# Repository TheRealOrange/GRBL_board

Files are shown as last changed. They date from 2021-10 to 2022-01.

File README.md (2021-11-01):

# GRBL_board

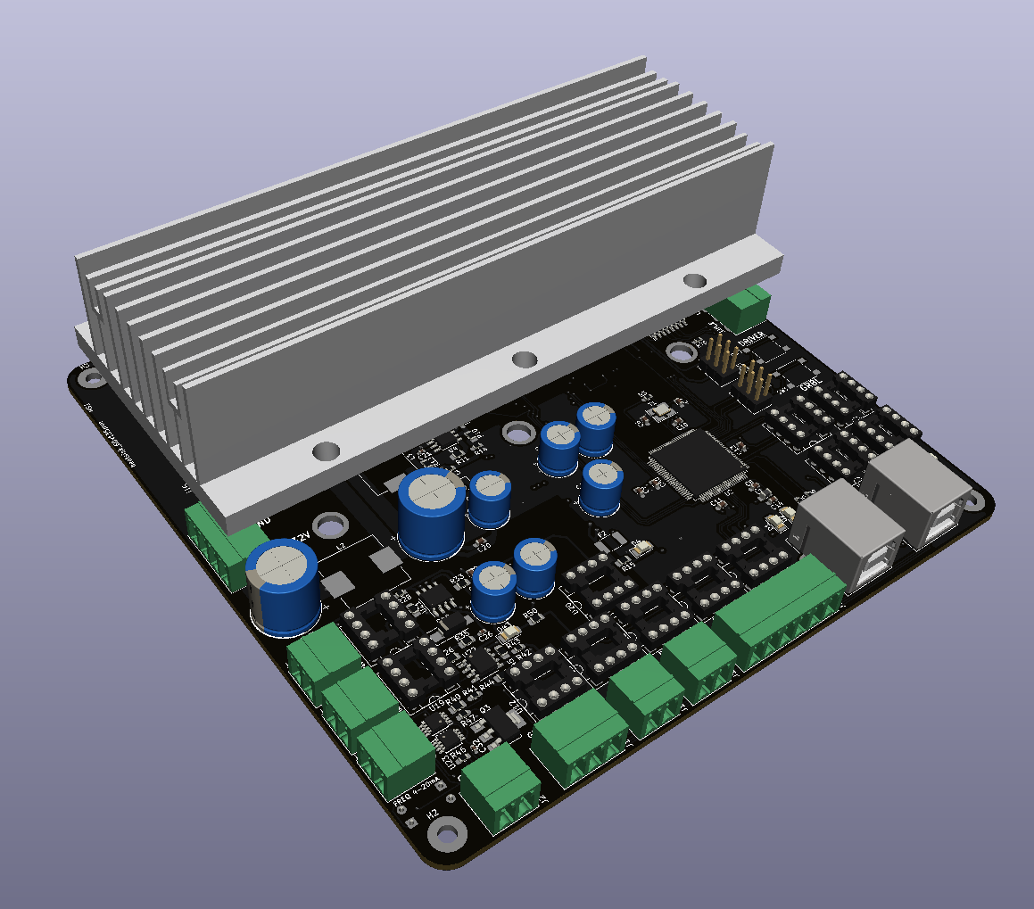
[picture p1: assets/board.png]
pcb picture


## Introduction

This is a PCB designed to run [GRBL](https://github.com/gnea/grbl), an open source CNC control software that is designed and optimised for Arduino. This board uses [GRBL-Mega](https://github.com/gnea/grbl-Mega), which is a version of GRBL that can run on the ATMEGA-2560, used in the Arduino Mega. This implementation allows GRBL to have a larger buffer size, since the ATMEGA-328P that GRBL was originally designed for has severe memory limitations.

This board design incorporates several additional features, such as:

- Designed for SPI configured Trinamic stepper drivers such as the TMC5160, TMC2130, etc.
- Ability to change the mirrored axis (X, Y or Z) via software (supports software configurable gantry levelling)
- All inputs and limit switch inputs wired with optocouplers, designed for normally open switches
- Onboard 12V 2A regulator, accepting 20-32VDC input
- Speed control for industrial VFDs, with a standard 4-20mA current loop for spindle speed control
- Sink logic for spindle control
- Possible sensorless homing using Trinamic drivers (not ideal since it only emulates a limit switch)

The goal is to accomplish this with minimal editing of the GRBL code, thus to do so an additional ATMEGA-328P is added on the board to enable the additional features.

## Connections

This board is designed with the aim of being as compatible as possible with the default GRBL, and as such, the pins are wired to follow the default GRBL-Mega pinout, as shown.
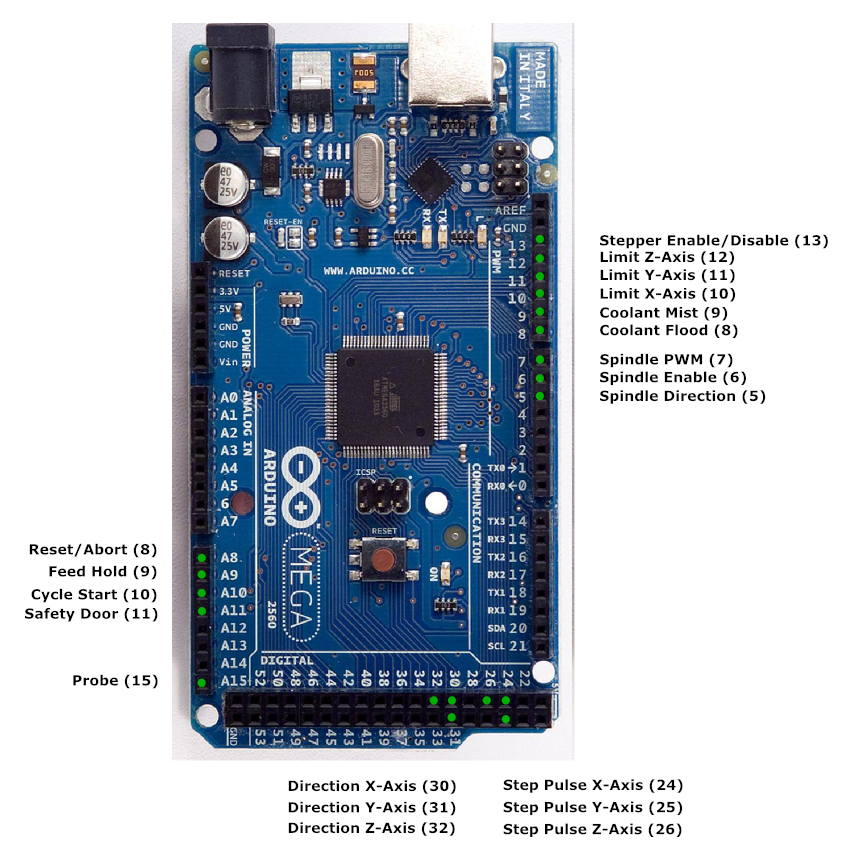
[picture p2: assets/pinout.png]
Default GRBL-Mega pinout


## Trinamic Drivers

Trinamic stepper motor drivers are exceptional in terms of performance and efficiency, incorporating advanced features that enable steppers to run cooler and with near silent operation. 

However, the tricky bit is that they are not a plug an play solution unlike other stepper drivers like the DRV8825 or the A4988 drivers. The drivers haveto be configured whenever they are powered up. To accomplish this, the separate ATMEGA-328P is used to communicate with the drivers via SPI in order to configure them.

## Mirrored Axis

Most CNC configurations include one axis which has dual stepper drive. GRBL has limited support for axis mirroring, and usually sacrifices some pins, such as spindle speed control. Thus, via the use of multiplexer ICs and the separate ATMEGA-328P, code can be uploaded to the ATMEGA-328P in order to specify which axis to mirror and whether to do gantry levelling for that axis.

To accomplish gantry levelling, the ATMEGA-328P will check the two limit switches on the mirrored axis, and if only one switch is triggered, the corresponding stepper's STEP pin will be held low, preventing it from moving until both switches are triggered. Once both limit switches are triggered, the limit switch signal will be sent to the GRBL controller running on the ATMEGA-2560.

## Inputs

Previously, I had an extremely bad experience with EMI on the limit switch lines when building a CNC, thus I decided to include an optocoupler on each input of the CNC controller. Although the switches are still normally open, the optocoupler requires current to drive the LED and thus it is nearly impossible for EMI to trigger the optocoupler. This should make the CNC much more robust against EMI, and it is possible to change the switches to normally closed by modifying GRBL.

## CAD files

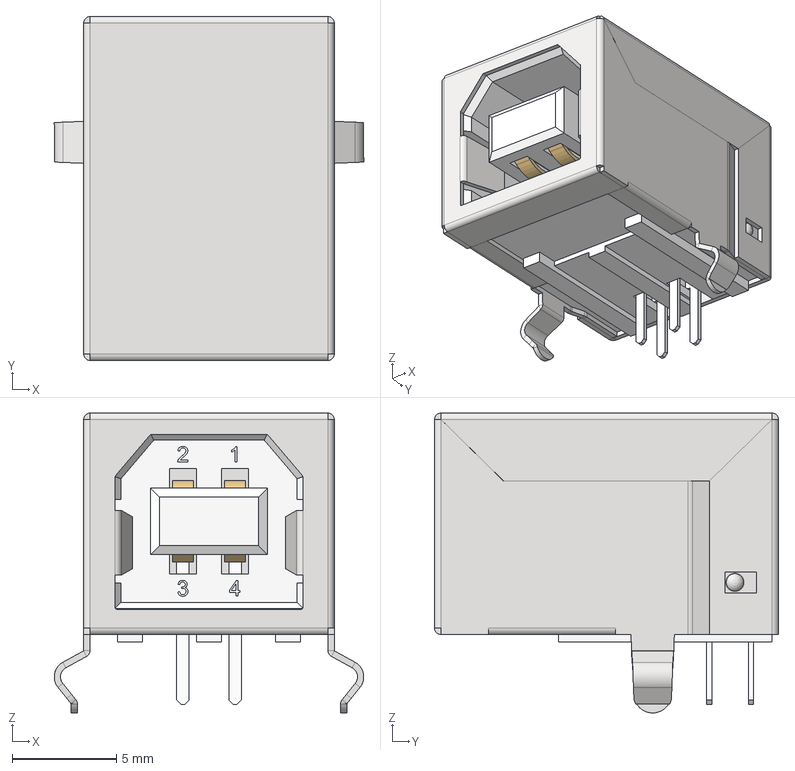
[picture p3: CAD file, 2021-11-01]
grbl_board/3d/USB_B_Horizontal.stp
14.8 x 16.5 x 14.4 mm

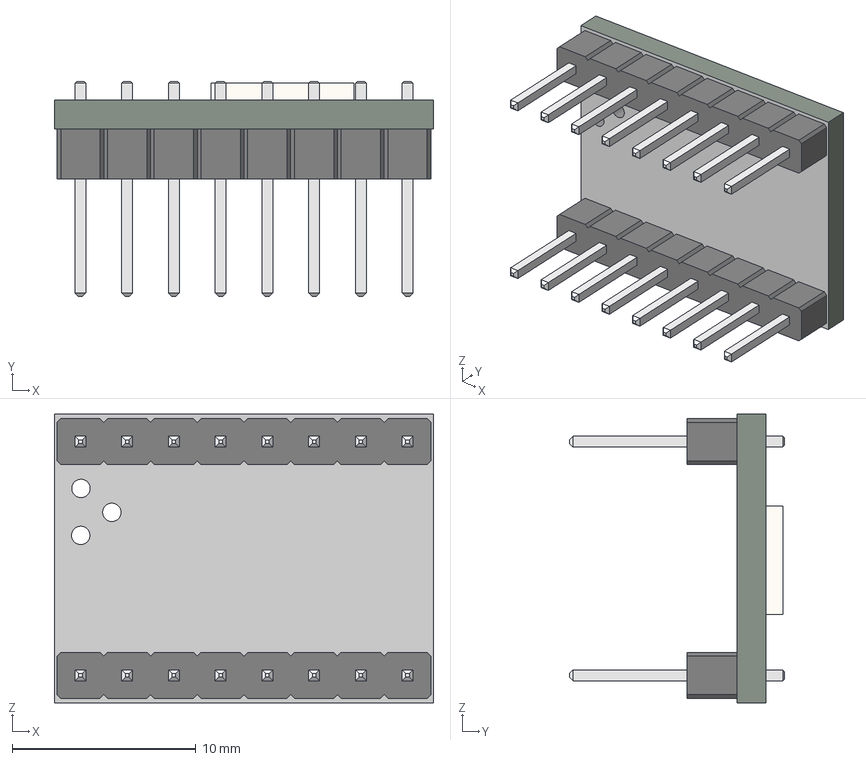
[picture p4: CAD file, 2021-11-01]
grbl_board/3d/SilentStepStick.step
20.6 x 11.7 x 15.7 mm

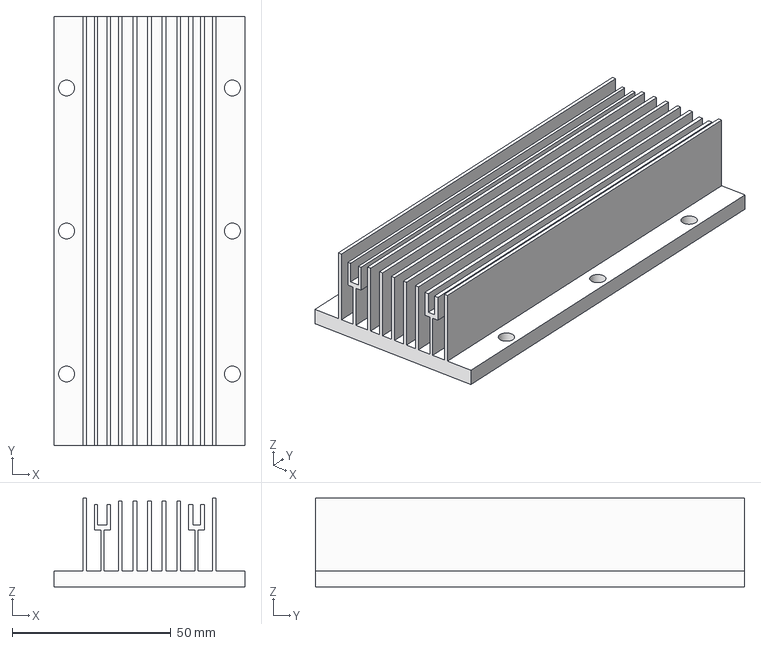
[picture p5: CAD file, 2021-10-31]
grbl_board/3d/heatsink_60x135mm_v1.step
60.0 x 135.0 x 28.0 mm

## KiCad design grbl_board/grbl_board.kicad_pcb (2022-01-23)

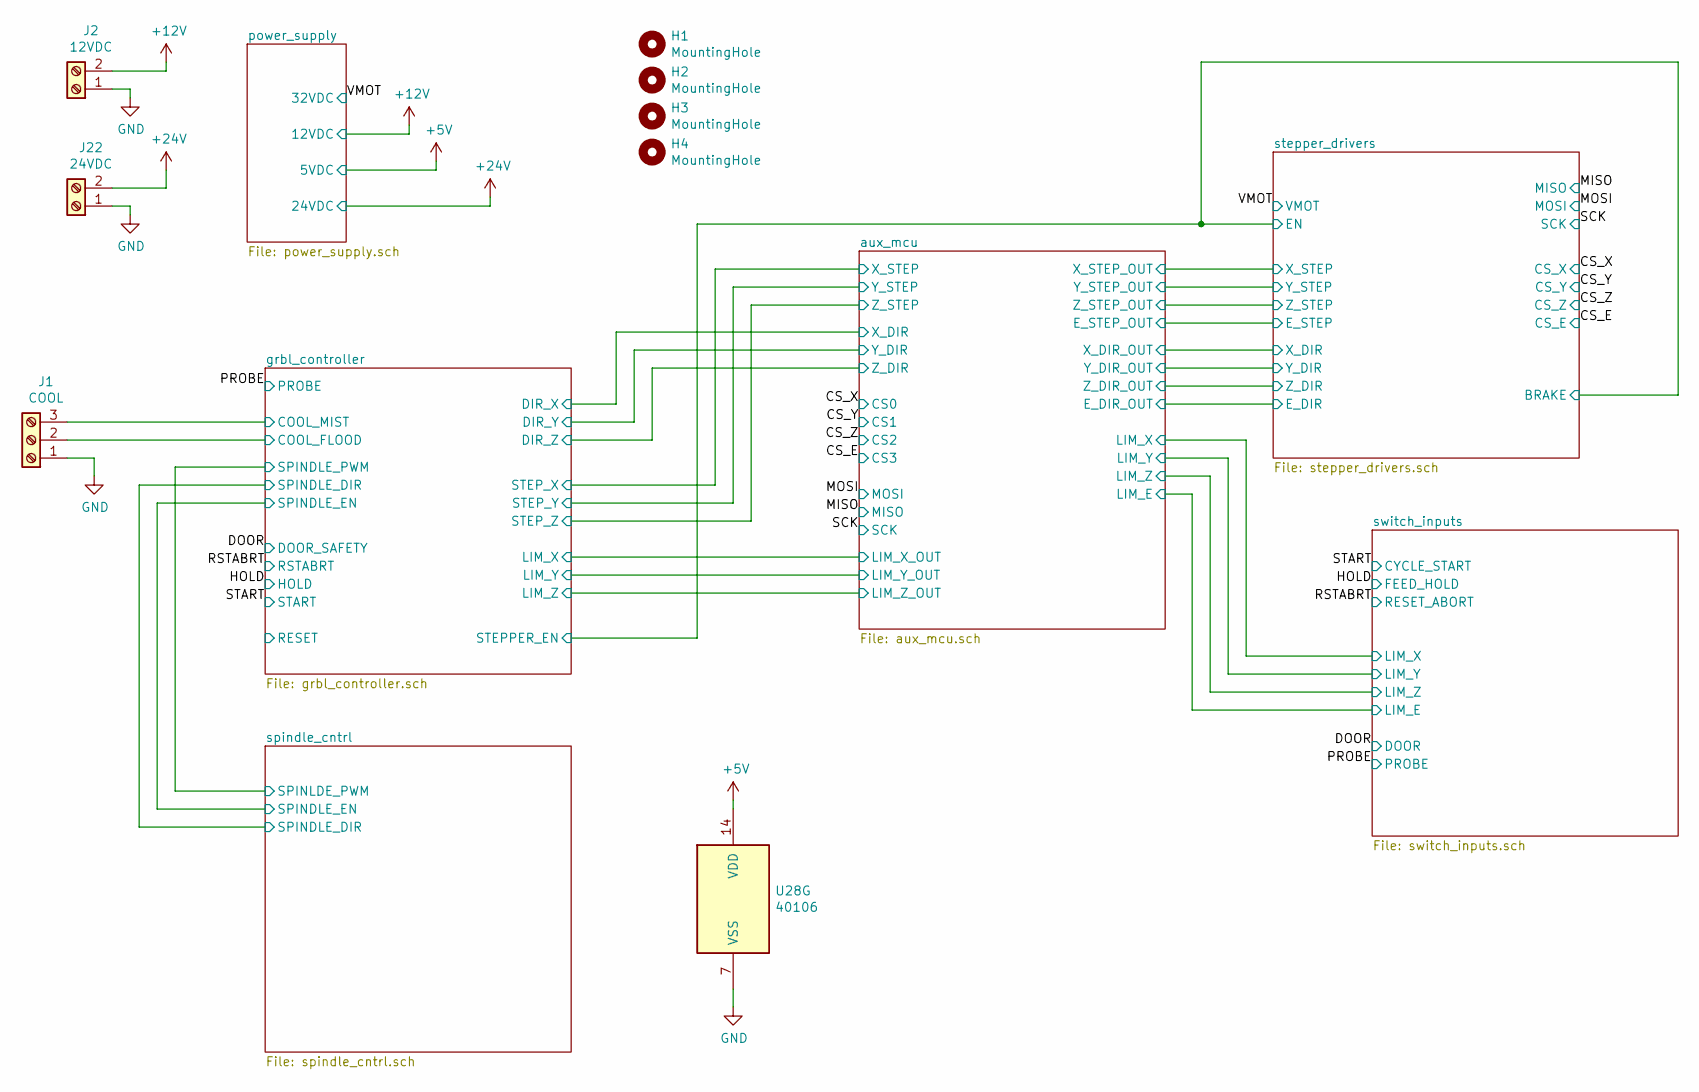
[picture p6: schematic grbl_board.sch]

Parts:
H1, H2, H3, H4: MountingHole; MountingHole_3.2mm_M3_Pad
J1: COOL; PhoenixContact_MC_1,5_3-G-3.81_1x03_P3.81mm_Horizontal; Digikey Part No. ED2809-ND
J2: 12VDC; PhoenixContact_MC_1,5_2-G-3.81_1x02_P3.81mm_Horizontal; Digikey Part No. ED2808-ND
J22: 24VDC; PhoenixContact_MC_1,5_2-G-3.81_1x02_P3.81mm_Horizontal; Digikey Part No. ED2808-ND
U28: 40106; TSSOP-14_4.4x5mm_P0.65mm; Digikey Part No. HEF40106BTT,112-ND

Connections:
+5V: U28.14 (VDD); also elsewhere on the board
+12V: J2.2; also elsewhere on the board
+24V: J22.2; also elsewhere on the board
/grbl_controller/COOL_FLOOD: J1.2; also elsewhere on the board
/grbl_controller/COOL_MIST: J1.3; also elsewhere on the board
GND: J1.1, J2.1, J22.1, U28.7 (VSS); also elsewhere on the board

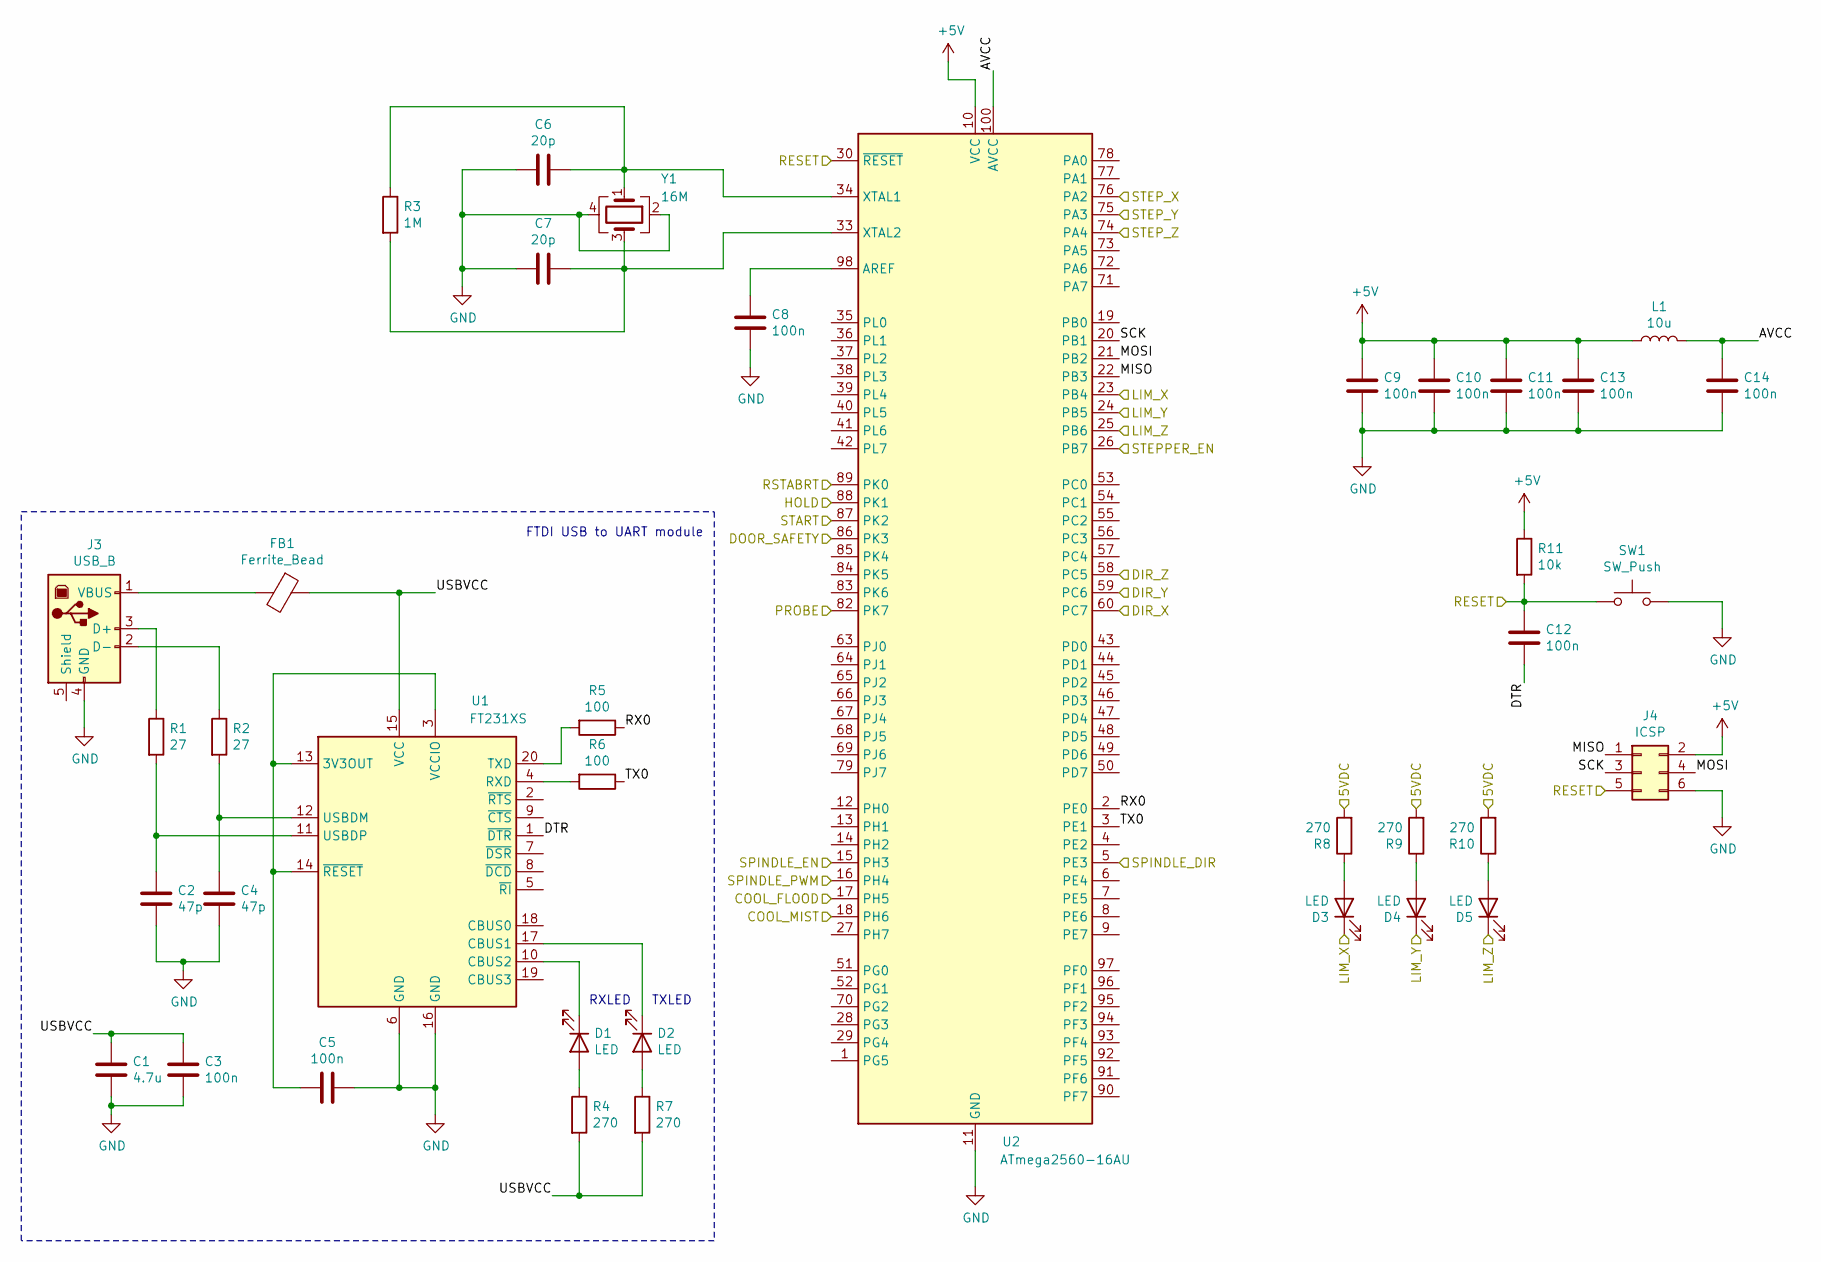
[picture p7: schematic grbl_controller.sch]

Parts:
C1: 4.7u; C_1206_3216Metric_Pad1.33x1.80mm_HandSolder; Digikey Part No. 1276-6781-1-ND
C2, C4: 47p; C_0402_1005Metric_Pad0.74x0.62mm_HandSolder; Digikey Part No. 1276-1699-1-ND
C3, C5, C8, C9, C10, C11, C12, C13, C14: 100n; C_0603_1608Metric_Pad1.05x0.95mm_HandSolder; Digikey Part No. 1276-1941-1-ND
C6, C7: 20p; C_0603_1608Metric_Pad1.05x0.95mm_HandSolder; Digikey Part No. 1276-1187-1-ND
D1, D2: LED; LED_1206_3216Metric_Pad1.42x1.75mm_HandSolder; Digikey Part No. 404-1042-1-ND
D3, D4, D5: LED; LED_1206_3216Metric_Pad1.42x1.75mm_HandSolder; Digikey Part No. 404-1046-1-ND
FB1: Ferrite_Bead; C_0603_1608Metric_Pad1.05x0.95mm_HandSolder; Digikey Part No. 732-1591-1-ND
J3: USB_B; USB_B_OST_USB-B1HSxx_Horizontal; Digikey Part No. 380-1492-ND
J4: ICSP; PinHeader_2x03_P2.54mm_Vertical; Digikey Part No. 609-3234-ND
L1: 10u; L_0805_2012Metric_Pad1.05x1.20mm_HandSolder; Digikey Part No. 490-4029-1-ND
R1, R2: 27; R_0603_1608Metric_Pad0.98x0.95mm_HandSolder; Digikey Part No. 311-27GRCT-ND
R3: 1M; R_0603_1608Metric_Pad0.98x0.95mm_HandSolder; Digikey Part No. 311-1.0MGRCT-ND
R4, R7, R8, R9, R10: 270; R_0805_2012Metric_Pad1.15x1.40mm_HandSolder; Digikey Part No. YAG6172CT-ND
R5, R6: 100; R_0603_1608Metric_Pad0.98x0.95mm_HandSolder; Digikey Part No. 311-100GRCT-ND
R11: 10k; R_0805_2012Metric_Pad1.15x1.40mm_HandSolder; Digikey Part No. 311-10KARCT-ND
SW1: SW_Push; SW_Push_1P1T_NO_6x6mm_H9.5mm; Digikey Part No. EG2526CT-ND
U1: FT231XS; SSOP-20_3.9x8.7mm_P0.635mm; Digikey Part No. 768-1129-1-ND
U2: ATmega2560-16AU; TQFP-100_14x14mm_P0.5mm; Digikey Part No. ATMEGA2560-16AU-ND
Y1: 16M; Crystal_SMD_SeikoEpson_TSX3225-4Pin_3.2x2.5mm_HandSoldering; Digikey Part No. SER4372CT-ND

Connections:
+5V: C9.1, C10.1, C11.1, C13.1, J4.2, L1.1, R11.1, U2.10 (VCC), U2.31 (VCC), U2.61 (VCC), U2.80 (VCC); also elsewhere on the board
/DOOR: U2.86 (PK3); also elsewhere on the board
/HOLD: U2.88 (PK1); also elsewhere on the board
/PROBE: U2.82 (PK7); also elsewhere on the board
/RSTABRT: U2.89 (PK0); also elsewhere on the board
/START: U2.87 (PK2); also elsewhere on the board
/grbl_controller/5VDC: R8.2, R9.2, R10.2
/grbl_controller/AVCC: C14.1, L1.2, U2.100 (AVCC)
/grbl_controller/COOL_FLOOD: U2.17 (PH5); also elsewhere on the board
/grbl_controller/COOL_MIST: U2.18 (PH6); also elsewhere on the board
/grbl_controller/DIR_X: U2.60 (PC7); also elsewhere on the board
/grbl_controller/DIR_Y: U2.59 (PC6); also elsewhere on the board
/grbl_controller/DIR_Z: U2.58 (PC5); also elsewhere on the board
/grbl_controller/DTR: C12.2, U1.1 (~DTR)
/grbl_controller/LIM_X: D3.1 (K), U2.23 (PB4); also elsewhere on the board
/grbl_controller/LIM_Y: D4.1 (K), U2.24 (PB5); also elsewhere on the board
/grbl_controller/LIM_Z: D5.1 (K), U2.25 (PB6); also elsewhere on the board
/grbl_controller/MISO: J4.1, U2.22 (PB3)
/grbl_controller/MOSI: J4.4, U2.21 (PB2)
/grbl_controller/RESET: C12.1, J4.5, R11.2, SW1.1, U2.30 (~RESET)
/grbl_controller/RX0: R5.1, U2.2 (PE0)
/grbl_controller/SCK: J4.3, U2.20 (PB1)
/grbl_controller/SPINDLE_DIR: U2.5 (PE3); also elsewhere on the board
/grbl_controller/SPINDLE_EN: U2.15 (PH3); also elsewhere on the board
/grbl_controller/SPINDLE_PWM: U2.16 (PH4); also elsewhere on the board
/grbl_controller/STEP_X: U2.76 (PA2); also elsewhere on the board
/grbl_controller/STEP_Y: U2.75 (PA3); also elsewhere on the board
/grbl_controller/STEP_Z: U2.74 (PA4); also elsewhere on the board
/grbl_controller/TX0: R6.1, U2.3 (PE1)
/grbl_controller/USBVCC: C1.1, C3.1, FB1.1, R4.2, R7.2, U1.15 (VCC)
/stepper_drivers/BRAKE: U2.26 (PB7); also elsewhere on the board
GND: C1.2, C2.2, C3.2, C4.2, C5.1, C6.2, C7.2, C8.1, C9.2, C10.2, C11.2, C13.2, C14.2, J3.4 (GND), J4.6, SW1.2, U1.6 (GND), U1.16 (GND), U2.11 (GND), U2.32 (GND), U2.62 (GND), U2.81 (GND), U2.99 (GND), Y1.2, Y1.4; also elsewhere on the board
unnamed: C2.1, R1.2, U1.11 (USBDP)
unnamed: C4.1, R2.2, U1.12 (USBDM)
unnamed: C5.2, U1.3 (VCCIO), U1.13 (3V3OUT), U1.14 (~RESET)
unnamed: C6.1, R3.1, U2.34 (XTAL1), Y1.1
unnamed: C7.1, R3.2, U2.33 (XTAL2), Y1.3
unnamed: C8.2, U2.98 (AREF)
unnamed: D1.1 (K), U1.10 (CBUS2)
unnamed: D1.2 (A), R4.1
unnamed: D2.1 (K), U1.17 (CBUS1)
unnamed: D2.2 (A), R7.1
unnamed: D3.2 (A), R8.1
unnamed: D4.2 (A), R9.1
unnamed: D5.2 (A), R10.1
unnamed: FB1.2, J3.1 (VBUS)
unnamed: J3.2 (D-), R2.1
unnamed: J3.3 (D+), R1.1
unnamed: R5.2, U1.20 (TXD)
unnamed: R6.2, U1.4 (RXD)

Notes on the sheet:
TXLED
RXLED
FTDI USB to UART module

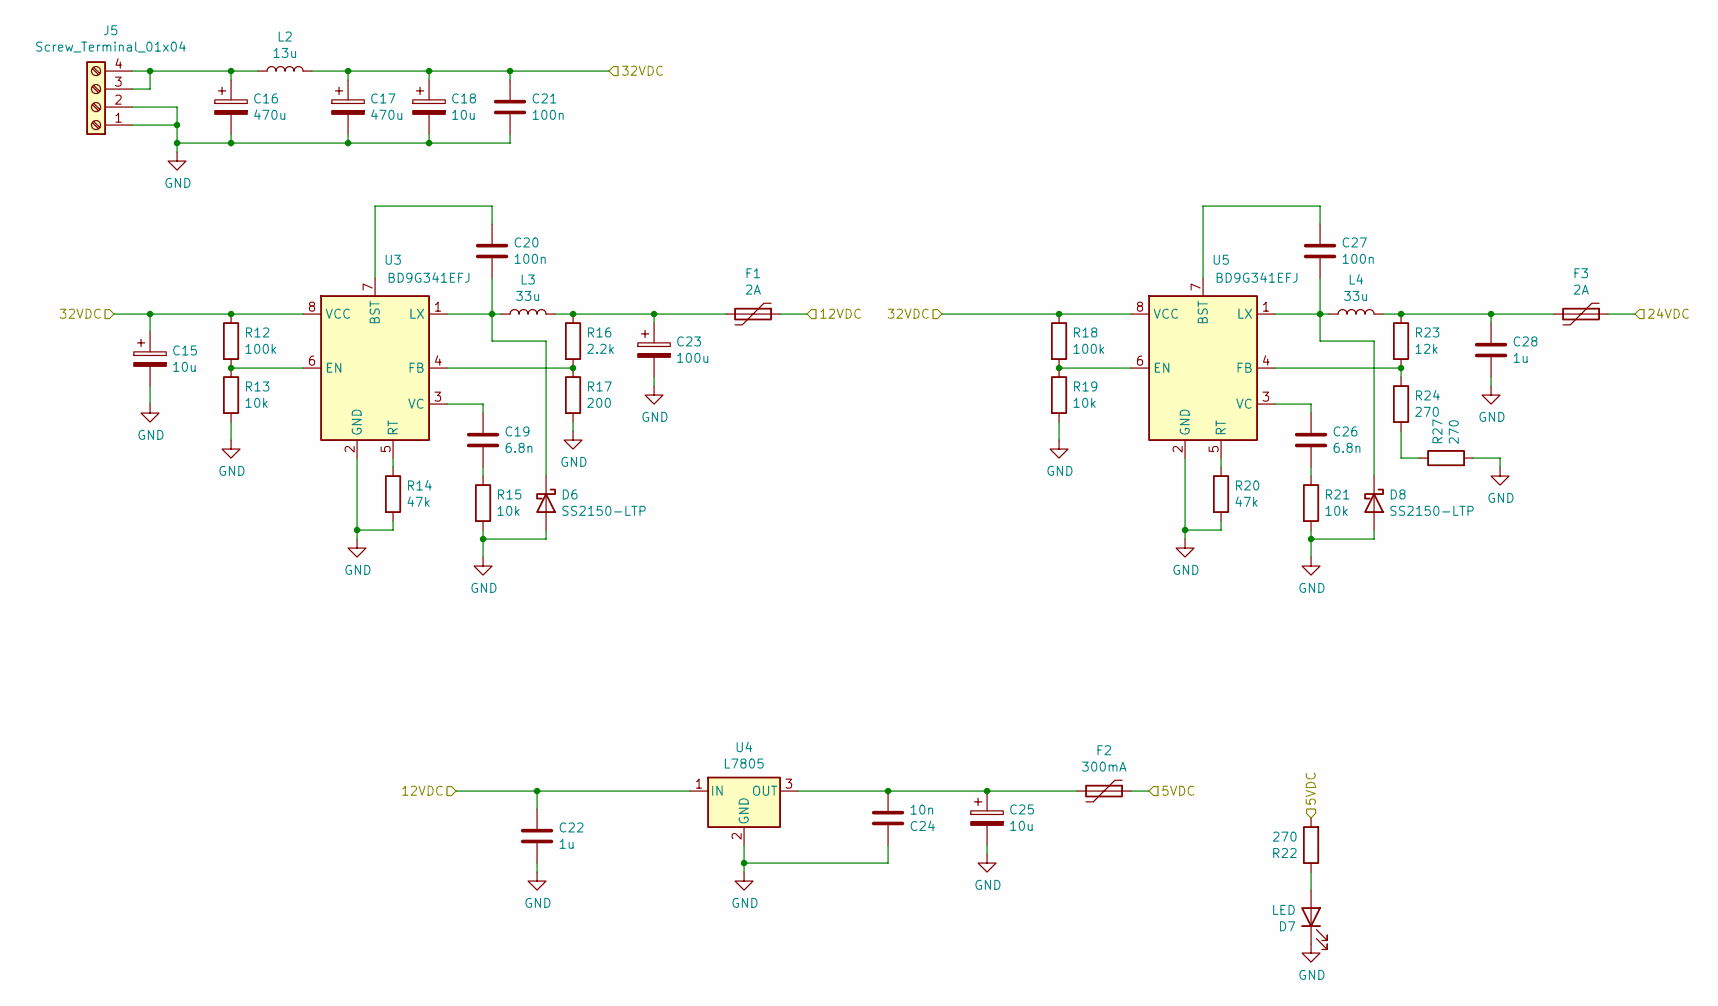
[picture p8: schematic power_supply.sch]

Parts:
C15, C18, C25: 10u; CP_Radial_D8.0mm_P3.50mm; Digikey Part No. 495-75596-ND
C16, C17: 470u; CP_Radial_D12.5mm_P5.00mm; Digikey Part No. 495-76603-ND
C19, C26: 6.8n; C_0402_1005Metric_Pad0.74x0.62mm_HandSolder; Digikey Part No. 1276-CL05B682KB5VPNCCT-ND
C20, C21, C27: 100n; C_0603_1608Metric_Pad1.05x0.95mm_HandSolder; Digikey Part No. 1276-1941-1-ND
C22, C28: 1u; C_1206_3216Metric_Pad1.33x1.80mm_HandSolder; Digikey Part No. 1276-1204-1-ND
C23: 100u; CP_Radial_D8.0mm_P3.50mm; Digikey Part No. 399-6119-ND
C24: 10n; C_0603_1608Metric_Pad1.08x0.95mm_HandSolder; Digikey Part No. 1276-1009-1-ND
D6, D8: SS2150-LTP; D_SMA_Handsoldering; Digikey Part No. SS2150-LTPMSCT-ND
D7: LED; LED_1206_3216Metric_Pad1.42x1.75mm_HandSolder; Digikey Part No. 404-1046-1-ND
F1, F3: 2A; Fuse_Bourns_MF-RHT200; Digikey Part No. 118-MF-RHT200/32-0-ND
F2: 300mA; Fuse_1812_4532Metric_Castellated; Digikey Part No. 507-1758-1-ND
J5: Screw_Terminal_01x04; PhoenixContact_MC_1,5_4-G-3.81_1x04_P3.81mm_Horizontal; Digikey Part No. ED2810-ND
L2: 13u; L_Wuerth_HCI-1365; Digikey Part No. 732-1140-1-ND
L3, L4: 33u; L_Vishay_IHLP-4040; Digikey Part No. 541-2273-1-ND
R12, R18: 100k; R_0603_1608Metric_Pad0.98x0.95mm_HandSolder; Digikey Part No. 311-100KGRCT-ND
R13, R15, R19, R21: 10k; R_0805_2012Metric_Pad1.15x1.40mm_HandSolder; Digikey Part No. 311-10KARCT-ND
R14, R20: 47k; R_0805_2012Metric_Pad1.15x1.40mm_HandSolder; Digikey Part No. 311-47KARCT-ND
R16: 2.2k; R_0603_1608Metric_Pad0.98x0.95mm_HandSolder; Digikey Part No. 311-2.2KGRCT-ND
R17: 200; R_0603_1608Metric_Pad0.98x0.95mm_HandSolder; Digikey Part No. 311-200GRCT-ND
R22, R24, R27: 270; R_0805_2012Metric_Pad1.15x1.40mm_HandSolder; Digikey Part No. YAG6172CT-ND
R23: 12k; R_0805_2012Metric_Pad1.15x1.40mm_HandSolder; Digikey Part No. 311-12KARCT-ND
U3, U5: BD9G341EFJ; HTSOP-8-1EP_3.9x4.9mm_P1.27mm_EP2.4x3.2mm_ThermalVias; Digikey Part No. BD9G341AEFJ-E2CT-ND
U4: L7805; TO-263-2; Digikey Part No. 497-1170-1-ND

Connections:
+5V: F2.1, R22.2; also elsewhere on the board
+12V: C22.1, F1.1, U4.1 (IN); also elsewhere on the board
+24V: F3.1; also elsewhere on the board
/VMOT: C15.1, C17.1, C18.1, C21.1, L2.2, R12.1, R18.1, U3.8 (VCC), U5.8 (VCC); also elsewhere on the board
GND: C15.2, C16.2, C17.2, C18.2, C21.2, C22.2, C23.2, C24.1, C25.2, C28.2, D6.2 (A), D7.1 (K), D8.2 (A), J5.1, J5.2, R13.2, R14.2, R15.2, R17.2, R19.2, R20.2, R21.2, R27.2, U3.2 (GND), U4.2 (GND), U5.2 (GND); also elsewhere on the board
unnamed: C16.1, J5.3, J5.4, L2.1
unnamed: C19.1, U3.3 (VC)
unnamed: C19.2, R15.1
unnamed: C20.1, U3.7 (BST)
unnamed: C20.2, D6.1 (K), L3.1, U3.1 (LX)
unnamed: C23.1, F1.2, L3.2, R16.1
unnamed: C24.2, C25.1, F2.2, U4.3 (OUT)
unnamed: C26.1, U5.3 (VC)
unnamed: C26.2, R21.1
unnamed: C27.1, U5.7 (BST)
unnamed: C27.2, D8.1 (K), L4.1, U5.1 (LX)
unnamed: C28.1, F3.2, L4.2, R23.1
unnamed: D7.2 (A), R22.1
unnamed: R12.2, R13.1, U3.6 (EN)
unnamed: R14.1, U3.5 (RT)
unnamed: R16.2, R17.1, U3.4 (FB)
unnamed: R18.2, R19.1, U5.6 (EN)
unnamed: R20.1, U5.5 (RT)
unnamed: R23.2, R24.1, U5.4 (FB)
unnamed: R24.2, R27.1

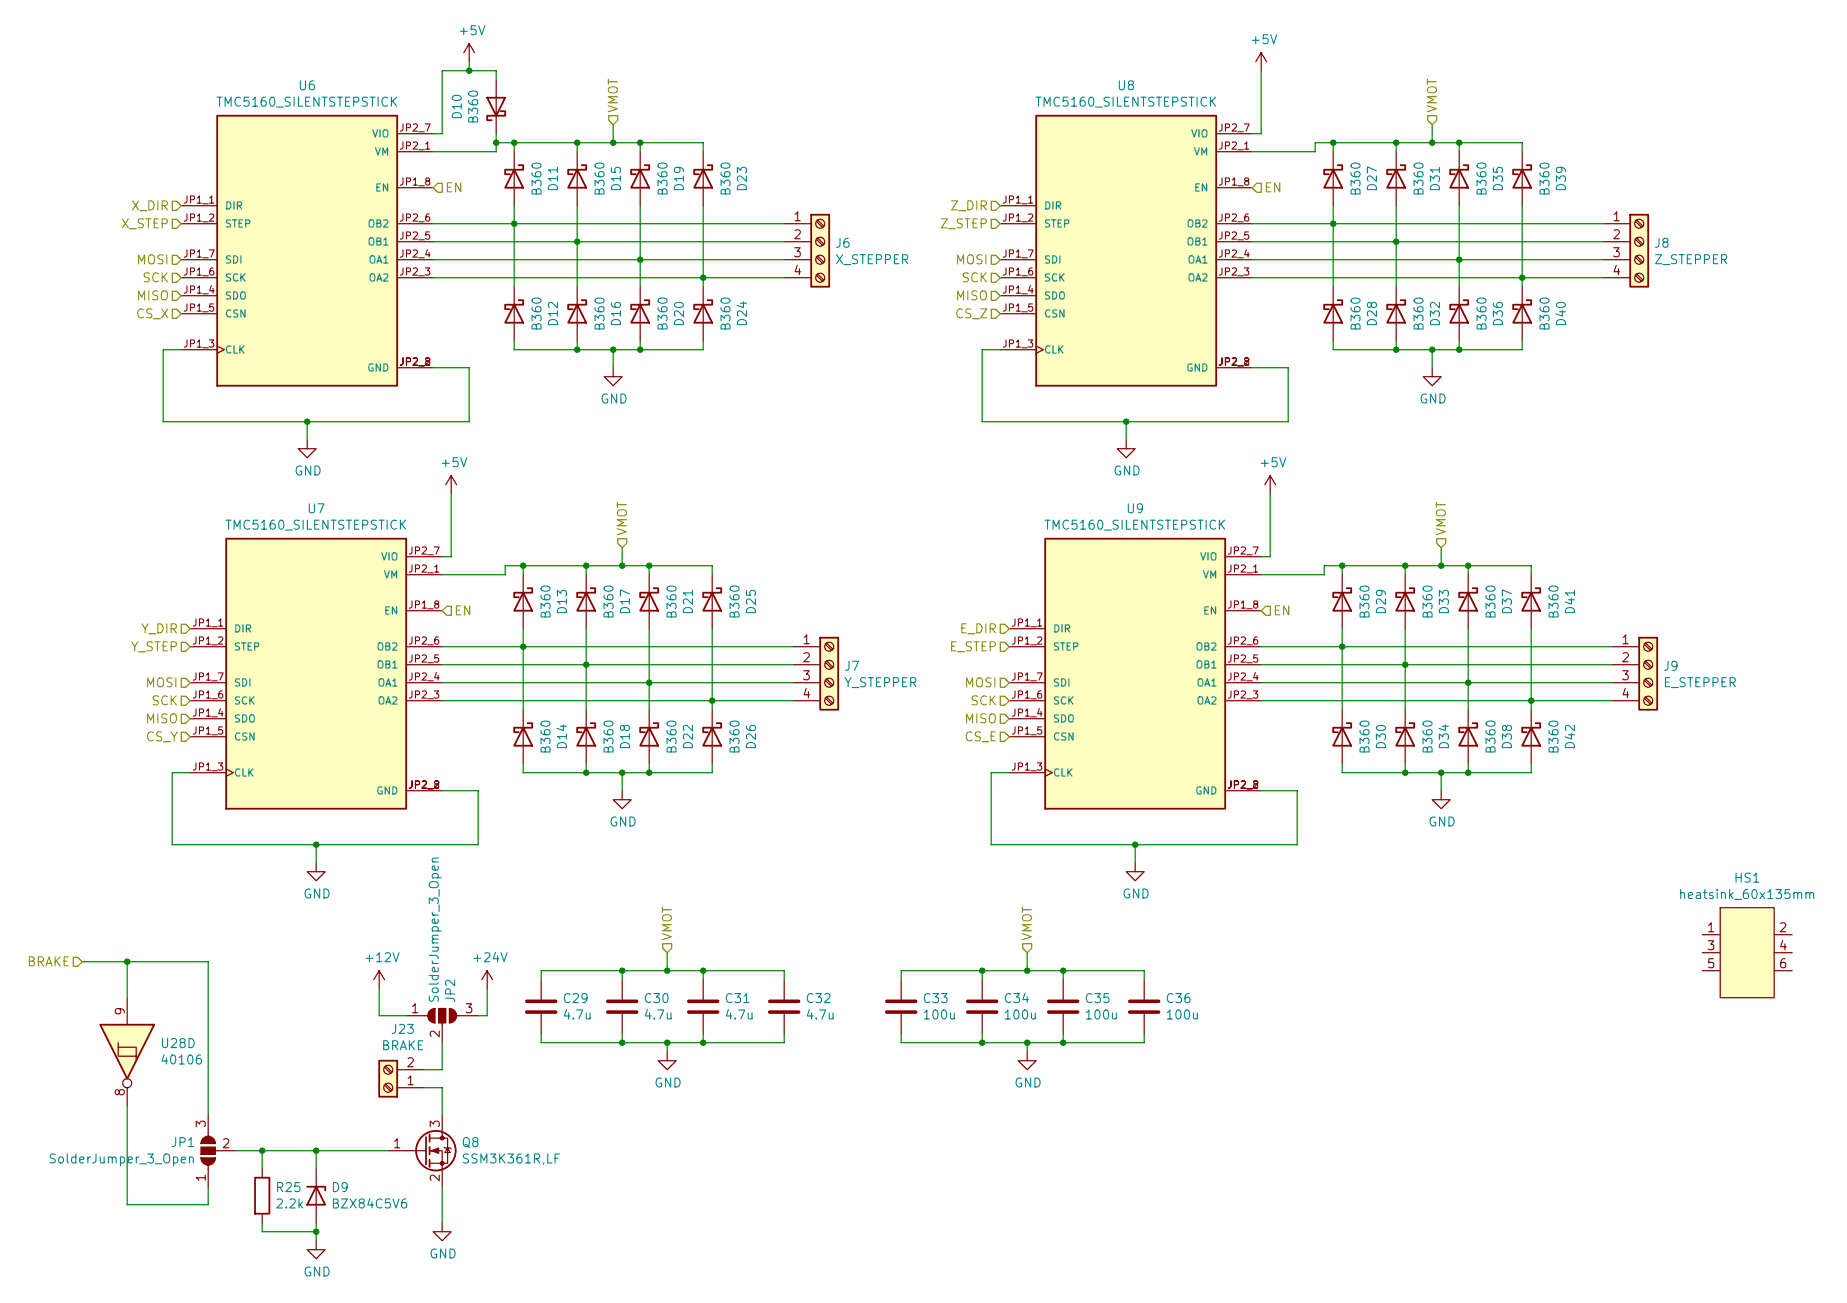
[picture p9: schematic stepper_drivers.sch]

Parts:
C29, C30, C31, C32: 4.7u; C_1206_3216Metric_Pad1.33x1.80mm_HandSolder; Digikey Part No. 1276-6781-1-ND
C33, C34, C35, C36: 100u; CP_Elec_8x10; Digikey Part No. UE107M050HFKTA
D9: BZX84C5V6; D_SOT-23_ANK; Digikey Part No. 1514-BZX84C5V6TRPBFREECT-ND
D10, D11, D12, D13, D14, D15, D16, D17, D18, D19, D20, D21, D22, D23, D24, D25, D26, D27, D28, D29, D30, D31, D32, D33, D34, D35, D36, D37, D38, D39, D40, D41, D42: B360; D_SMA_Handsoldering; Digikey Part No. CD214A-B360RCT-ND
HS1: heatsink_60x135mm
J6: X_STEPPER; PhoenixContact_MC_1,5_4-G-3.81_1x04_P3.81mm_Horizontal; Digikey Part No. ED2810-ND
J7: Y_STEPPER; PhoenixContact_MC_1,5_4-G-3.81_1x04_P3.81mm_Horizontal; Digikey Part No. ED2810-ND
J8: Z_STEPPER; PhoenixContact_MC_1,5_4-G-3.81_1x04_P3.81mm_Horizontal; Digikey Part No. ED2810-ND
J9: E_STEPPER; PhoenixContact_MC_1,5_4-G-3.81_1x04_P3.81mm_Horizontal; Digikey Part No. ED2810-ND
J23: BRAKE; PhoenixContact_MC_1,5_2-G-3.81_1x02_P3.81mm_Horizontal; Digikey Part No. ED2808-ND
JP1, JP2: SolderJumper_3_Open; SolderJumper-3_P1.3mm_Open_RoundedPad1.0x1.5mm
Q8: SSM3K361R,LF; SOT-23; Digikey Part No. SSM3K361RLFCT-ND
R25: 2.2k; R_0603_1608Metric_Pad0.98x0.95mm_HandSolder; Digikey Part No. 311-2.2KGRCT-ND
U6, U7, U8, U9: TMC5160_SILENTSTEPSTICK; PARTREV v11; Digikey Part No. 1460-TMC5160SILENTSTEPSTICK-ND
U28: 40106

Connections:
+5V: D10.2 (A), U6.JP2_7 (VIO), U7.JP2_7 (VIO), U8.JP2_7 (VIO), U9.JP2_7 (VIO); also elsewhere on the board
+12V: JP2.1 (A); also elsewhere on the board
+24V: JP2.3 (B); also elsewhere on the board
/CS_E: U9.JP1_5 (CSN); also elsewhere on the board
/CS_X: U6.JP1_5 (CSN); also elsewhere on the board
/CS_Y: U7.JP1_5 (CSN); also elsewhere on the board
/CS_Z: U8.JP1_5 (CSN); also elsewhere on the board
/MISO: U6.JP1_4 (SDO), U7.JP1_4 (SDO), U8.JP1_4 (SDO), U9.JP1_4 (SDO); also elsewhere on the board
/MOSI: U6.JP1_7 (SDI), U7.JP1_7 (SDI), U8.JP1_7 (SDI), U9.JP1_7 (SDI); also elsewhere on the board
/SCK: U6.JP1_6 (SCK), U7.JP1_6 (SCK), U8.JP1_6 (SCK), U9.JP1_6 (SCK); also elsewhere on the board
/VMOT: C29.1, C30.1, C31.1, C32.1, C33.1, C34.1, C35.1, C36.1, D10.1 (K), D11.1 (K), D13.1 (K), D15.1 (K), D17.1 (K), D19.1 (K), D21.1 (K), D23.1 (K), D25.1 (K), D27.1 (K), D29.1 (K), D31.1 (K), D33.1 (K), D35.1 (K), D37.1 (K), D39.1 (K), D41.1 (K), U6.JP2_1 (VM), U7.JP2_1 (VM), U8.JP2_1 (VM), U9.JP2_1 (VM); also elsewhere on the board
/grbl_controller/DIR_X: U6.JP1_1 (DIR); also elsewhere on the board
/grbl_controller/DIR_Y: U7.JP1_1 (DIR); also elsewhere on the board
/grbl_controller/DIR_Z: U8.JP1_1 (DIR); also elsewhere on the board
/stepper_drivers/BRAKE: JP1.3 (B), U6.JP1_8 (EN), U7.JP1_8 (EN), U8.JP1_8 (EN), U9.JP1_8 (EN), U28.9; also elsewhere on the board
/stepper_drivers/E_DIR: U9.JP1_1 (DIR); also elsewhere on the board
/stepper_drivers/E_STEP: U9.JP1_2 (STEP); also elsewhere on the board
/stepper_drivers/X_STEP: U6.JP1_2 (STEP); also elsewhere on the board
/stepper_drivers/Y_STEP: U7.JP1_2 (STEP); also elsewhere on the board
/stepper_drivers/Z_STEP: U8.JP1_2 (STEP); also elsewhere on the board
GND: C29.2, C30.2, C31.2, C32.2, C33.2, C34.2, C35.2, C36.2, D9.2 (A), D12.2 (A), D14.2 (A), D16.2 (A), D18.2 (A), D20.2 (A), D22.2 (A), D24.2 (A), D26.2 (A), D28.2 (A), D30.2 (A), D32.2 (A), D34.2 (A), D36.2 (A), D38.2 (A), D40.2 (A), D42.2 (A), Q8.2 (S), R25.2, U6.JP1_3 (CLK), U6.JP2_2 (GND), U6.JP2_8 (GND), U7.JP1_3 (CLK), U7.JP2_2 (GND), U7.JP2_8 (GND), U8.JP1_3 (CLK), U8.JP2_2 (GND), U8.JP2_8 (GND), U9.JP1_3 (CLK), U9.JP2_2 (GND), U9.JP2_8 (GND); also elsewhere on the board
unnamed: D9.1 (K), JP1.2 (C), Q8.1 (G), R25.1
unnamed: D11.2 (A), D12.1 (K), J6.1, U6.JP2_6 (OB2)
unnamed: D13.2 (A), D14.1 (K), J7.1, U7.JP2_6 (OB2)
unnamed: D15.2 (A), D16.1 (K), J6.2, U6.JP2_5 (OB1)
unnamed: D17.2 (A), D18.1 (K), J7.2, U7.JP2_5 (OB1)
unnamed: D19.2 (A), D20.1 (K), J6.3, U6.JP2_4 (OA1)
unnamed: D21.2 (A), D22.1 (K), J7.3, U7.JP2_4 (OA1)
unnamed: D23.2 (A), D24.1 (K), J6.4, U6.JP2_3 (OA2)
unnamed: D25.2 (A), D26.1 (K), J7.4, U7.JP2_3 (OA2)
unnamed: D27.2 (A), D28.1 (K), J8.1, U8.JP2_6 (OB2)
unnamed: D29.2 (A), D30.1 (K), J9.1, U9.JP2_6 (OB2)
unnamed: D31.2 (A), D32.1 (K), J8.2, U8.JP2_5 (OB1)
unnamed: D33.2 (A), D34.1 (K), J9.2, U9.JP2_5 (OB1)
unnamed: D35.2 (A), D36.1 (K), J8.3, U8.JP2_4 (OA1)
unnamed: D37.2 (A), D38.1 (K), J9.3, U9.JP2_4 (OA1)
unnamed: D39.2 (A), D40.1 (K), J8.4, U8.JP2_3 (OA2)
unnamed: D41.2 (A), D42.1 (K), J9.4, U9.JP2_3 (OA2)
unnamed: J23.1, Q8.3 (D)
unnamed: J23.2, JP2.2 (C)
unnamed: JP1.1 (A), U28.8

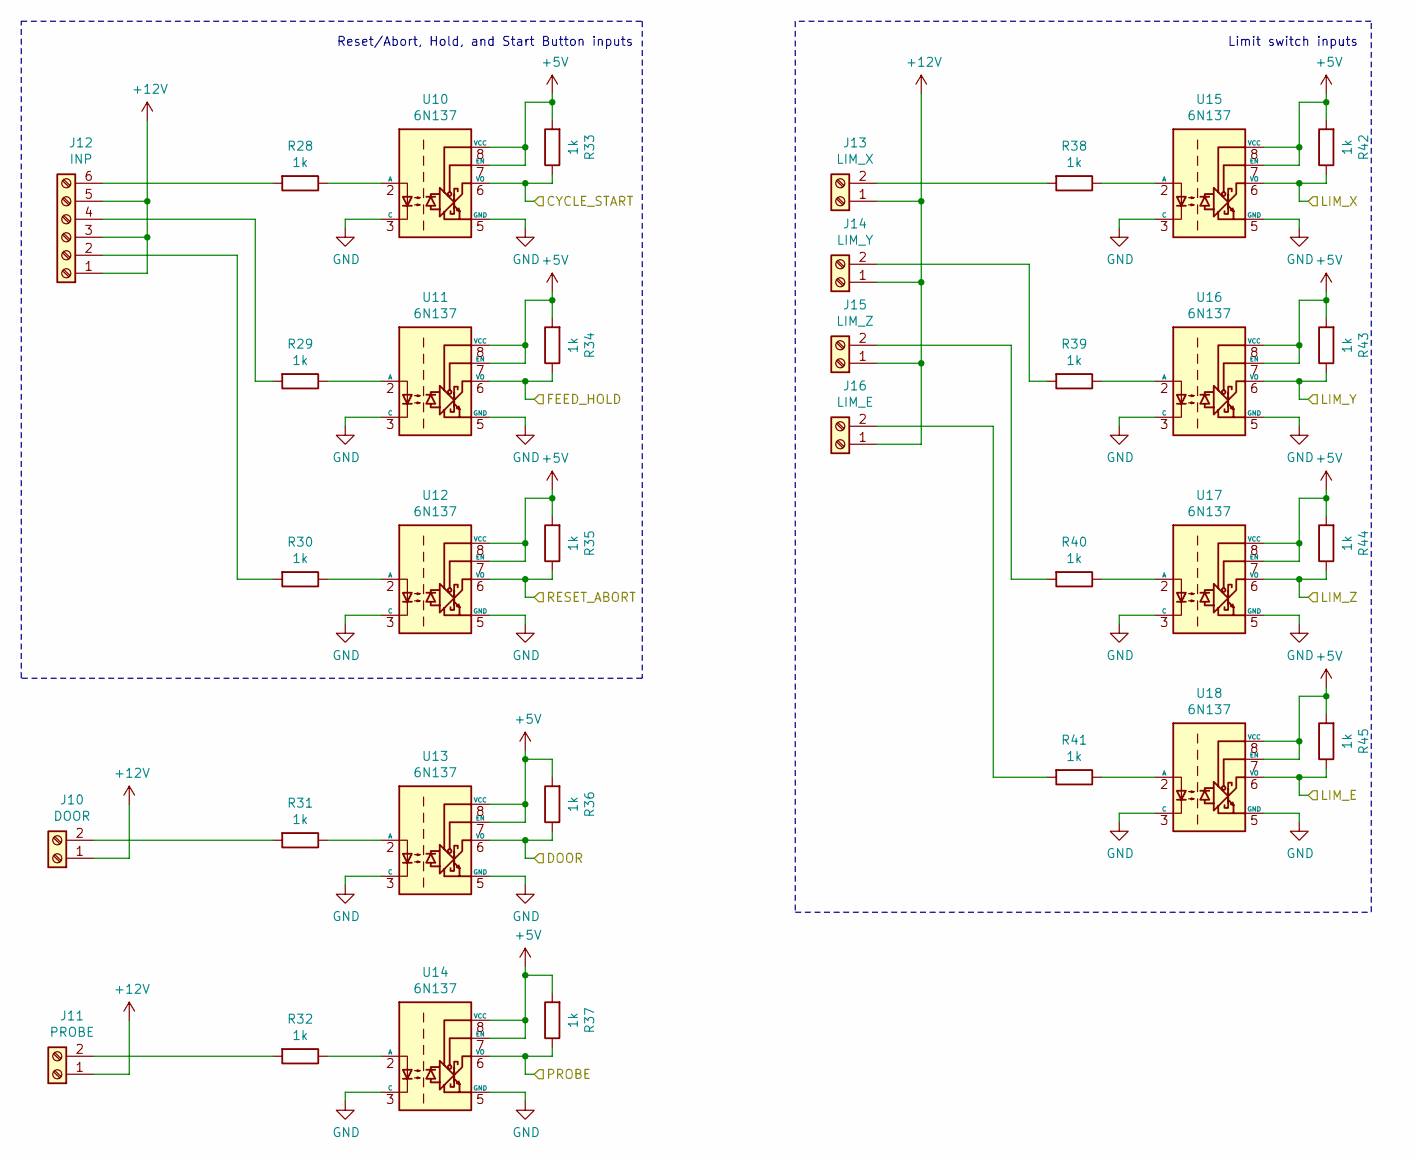
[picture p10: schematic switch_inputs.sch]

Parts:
J10: DOOR; PhoenixContact_MC_1,5_2-G-3.81_1x02_P3.81mm_Horizontal; Digikey Part No. ED2808-ND
J11: PROBE; PhoenixContact_MC_1,5_2-G-3.81_1x02_P3.81mm_Horizontal; Digikey Part No. ED2808-ND
J12: INP; PhoenixContact_MC_1,5_6-G-3.81_1x06_P3.81mm_Horizontal; Digikey Part No. ED2812-ND
J13: LIM_X; PhoenixContact_MC_1,5_2-G-3.81_1x02_P3.81mm_Horizontal; Digikey Part No. ED2808-ND
J14: LIM_Y; PhoenixContact_MC_1,5_2-G-3.81_1x02_P3.81mm_Horizontal; Digikey Part No. ED2808-ND
J15: LIM_Z; PhoenixContact_MC_1,5_2-G-3.81_1x02_P3.81mm_Horizontal; Digikey Part No. ED2808-ND
J16: LIM_E; PhoenixContact_MC_1,5_2-G-3.81_1x02_P3.81mm_Horizontal; Digikey Part No. ED2808-ND
R28, R29, R30, R31, R32, R38, R39, R40, R41: 1k; R_1206_3216Metric_Pad1.30x1.75mm_HandSolder; Digikey Part No. 311-1.0KERCT-ND
R33, R34, R35, R36, R37, R42, R43, R44, R45: 1k; R_0805_2012Metric_Pad1.15x1.40mm_HandSolder; Digikey Part No. 311-10KARCT-ND
U10, U11, U12, U13, U14, U15, U16, U17, U18: 6N137; DIP-8_W7.62mm_Socket; Digikey Part No. 6N137IS-ND

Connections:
+5V: R33.2, R34.2, R35.2, R36.2, R37.2, R42.2, R43.2, R44.2, R45.2, U10.7 (EN), U10.8 (VCC), U11.7 (EN), U11.8 (VCC), U12.7 (EN), U12.8 (VCC), U13.7 (EN), U13.8 (VCC), U14.7 (EN), U14.8 (VCC), U15.7 (EN), U15.8 (VCC), U16.7 (EN), U16.8 (VCC), U17.7 (EN), U17.8 (VCC), U18.7 (EN), U18.8 (VCC); also elsewhere on the board
+12V: J10.1, J11.1, J12.1, J12.3, J12.5, J13.1, J14.1, J15.1, J16.1; also elsewhere on the board
/DOOR: R36.1, U13.6 (VO); also elsewhere on the board
/HOLD: R34.1, U11.6 (VO); also elsewhere on the board
/PROBE: R37.1, U14.6 (VO); also elsewhere on the board
/RSTABRT: R35.1, U12.6 (VO); also elsewhere on the board
/START: R33.1, U10.6 (VO); also elsewhere on the board
/aux_mcu/LIM_E: R45.1, U18.6 (VO); also elsewhere on the board
/aux_mcu/LIM_X: R42.1, U15.6 (VO); also elsewhere on the board
/aux_mcu/LIM_Y: R43.1, U16.6 (VO); also elsewhere on the board
/aux_mcu/LIM_Z: R44.1, U17.6 (VO); also elsewhere on the board
GND: U10.3 (C), U10.5 (GND), U11.3 (C), U11.5 (GND), U12.3 (C), U12.5 (GND), U13.3 (C), U13.5 (GND), U14.3 (C), U14.5 (GND), U15.3 (C), U15.5 (GND), U16.3 (C), U16.5 (GND), U17.3 (C), U17.5 (GND), U18.3 (C), U18.5 (GND); also elsewhere on the board
unnamed: J10.2, R31.2
unnamed: J11.2, R32.2
unnamed: J12.2, R30.2
unnamed: J12.4, R29.2
unnamed: J12.6, R28.2
unnamed: J13.2, R38.2
unnamed: J14.2, R39.2
unnamed: J15.2, R40.2
unnamed: J16.2, R41.2
unnamed: R28.1, U10.2 (A)
unnamed: R29.1, U11.2 (A)
unnamed: R30.1, U12.2 (A)
unnamed: R31.1, U13.2 (A)
unnamed: R32.1, U14.2 (A)
unnamed: R38.1, U15.2 (A)
unnamed: R39.1, U16.2 (A)
unnamed: R40.1, U17.2 (A)
unnamed: R41.1, U18.2 (A)

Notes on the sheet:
Limit switch inputs
Reset/Abort, Hold, and Start Button inputs

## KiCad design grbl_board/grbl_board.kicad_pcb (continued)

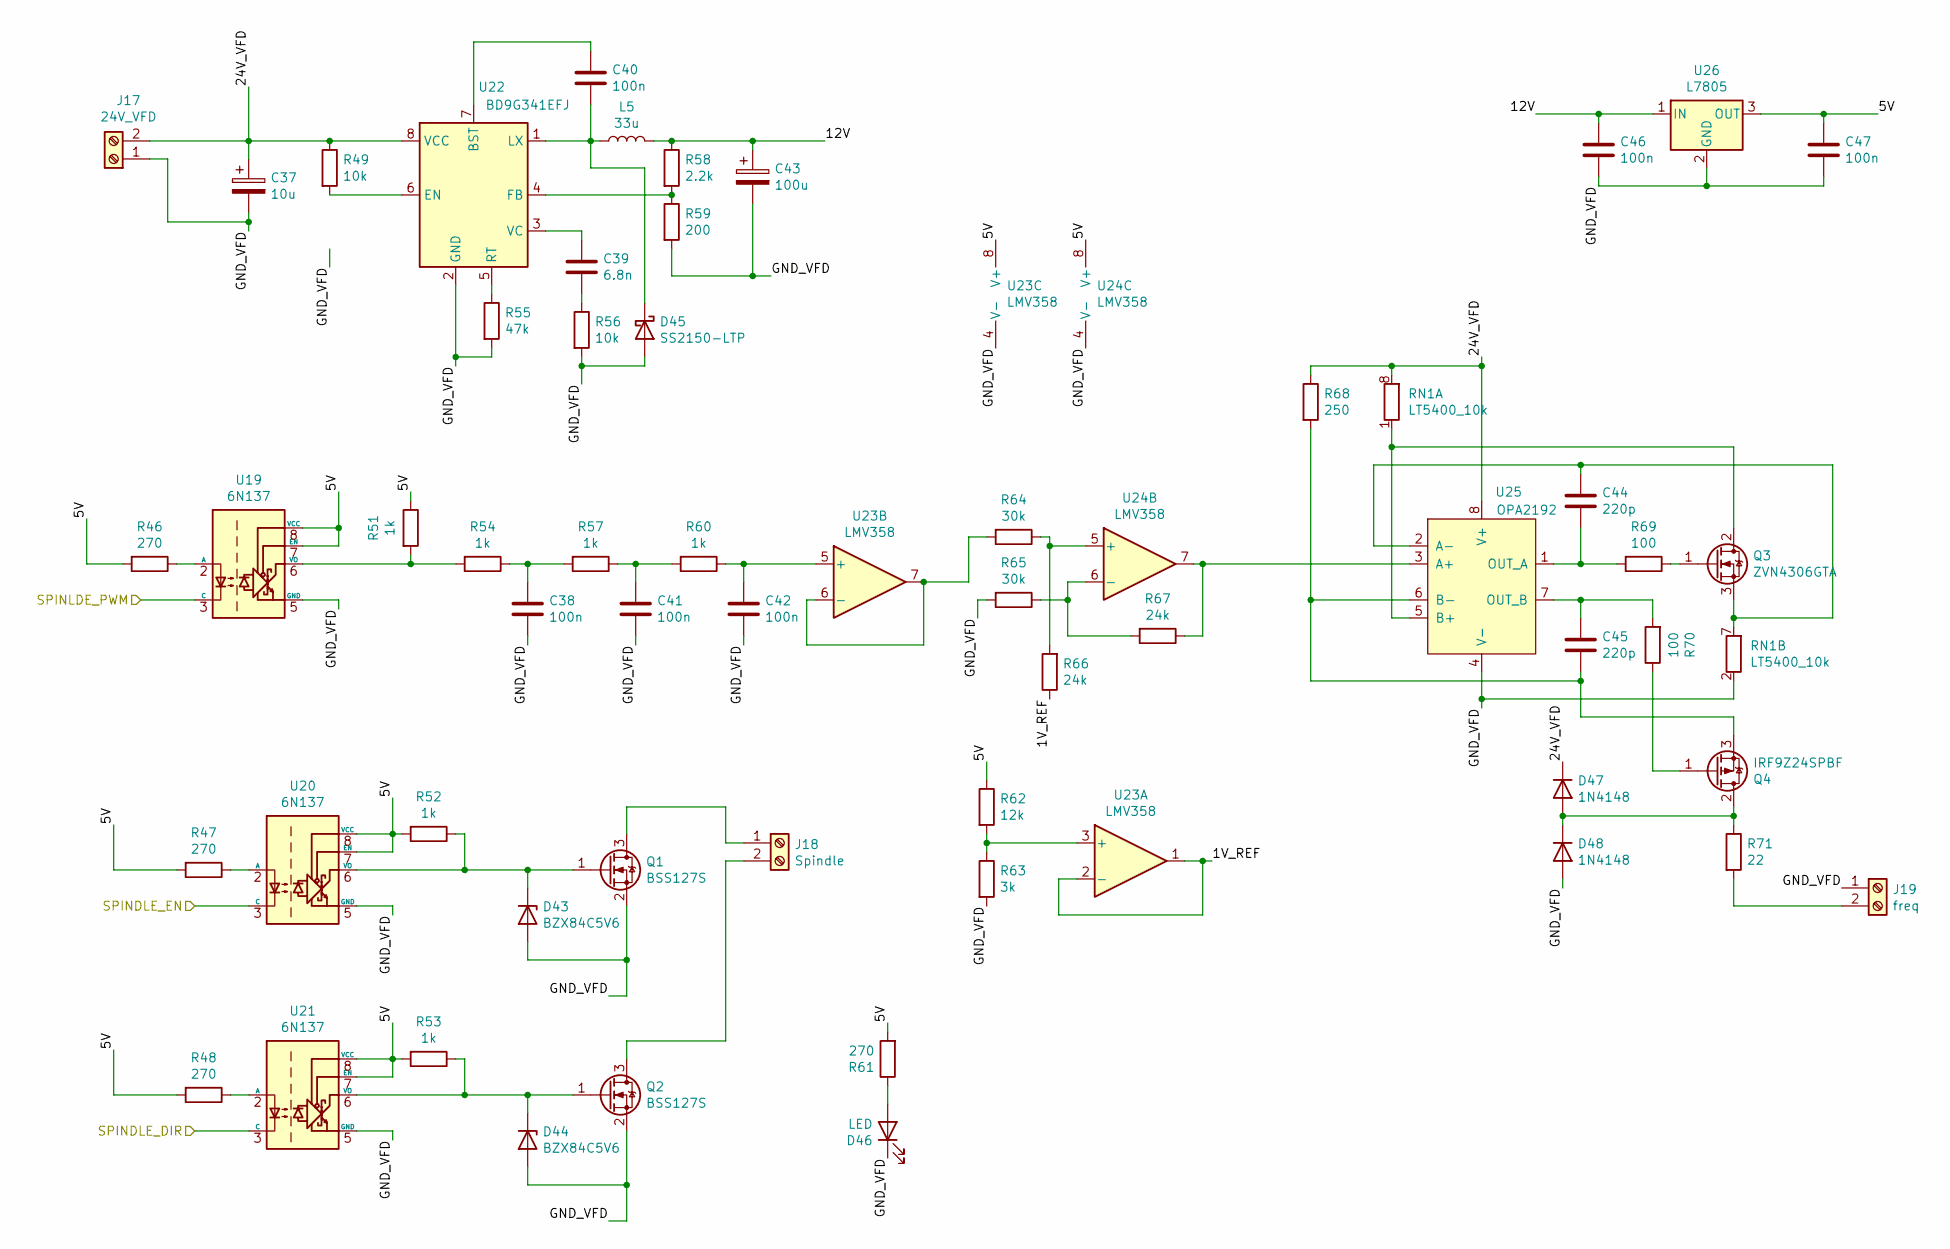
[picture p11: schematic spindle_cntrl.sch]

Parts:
C37: 10u; CP_Radial_D8.0mm_P3.50mm; Digikey Part No. 495-75596-ND
C38, C40, C41, C42, C46, C47: 100n; C_0603_1608Metric_Pad1.05x0.95mm_HandSolder; Digikey Part No. 1276-1941-1-ND
C39: 6.8n; C_0402_1005Metric_Pad0.74x0.62mm_HandSolder; Digikey Part No. 1276-CL05B682KB5VPNCCT-ND
C43: 100u; CP_Radial_D8.0mm_P3.50mm; Digikey Part No. 399-6119-ND
C44, C45: 220p; C_0402_1005Metric_Pad0.74x0.62mm_HandSolder; Digikey Part No. 1276-1059-1-ND
D43, D44: BZX84C5V6; D_SOT-23_ANK; Digikey Part No. 1514-BZX84C5V6TRPBFREECT-ND
D45: SS2150-LTP; D_SMA_Handsoldering; Digikey Part No. SS2150-LTPMSCT-ND
D46: LED; LED_1206_3216Metric_Pad1.42x1.75mm_HandSolder; Digikey Part No. 404-1046-1-ND
D47, D48: 1N4148; D_DO-35_SOD27_P7.62mm_Horizontal; Digikey Part No. 1N4148FS-ND
J17: 24V_VFD; PhoenixContact_MC_1,5_2-G-3.81_1x02_P3.81mm_Horizontal; Digikey Part No. ED2808-ND
J18: Spindle; PhoenixContact_MC_1,5_2-G-3.81_1x02_P3.81mm_Horizontal; Digikey Part No. ED2808-ND
J19: freq; PhoenixContact_MC_1,5_2-G-3.81_1x02_P3.81mm_Horizontal; Digikey Part No. ED2808-ND
L5: 33u; L_Vishay_IHLP-4040; Digikey Part No. 541-2273-1-ND
Q1, Q2: BSS127S; SOT-23; Digikey Part No. BSS127S-7DICT-ND
Q3: ZVN4306GTA; SOT-223-3_TabPin2; Digikey Part No. ZVN4306GCT-ND
Q4: IRF9Z24SPBF; TO-263-3_TabPin2; Digikey Part No. IRF9Z24SPBF-ND
R46, R47, R48, R61: 270; R_0805_2012Metric_Pad1.15x1.40mm_HandSolder; Digikey Part No. YAG6172CT-ND
R49, R56: 10k; R_0805_2012Metric_Pad1.15x1.40mm_HandSolder; Digikey Part No. 311-10KARCT-ND
R51, R52, R53, R54, R57, R60: 1k; R_0805_2012Metric_Pad1.15x1.40mm_HandSolder; Digikey Part No. 311-10KARCT-ND
R55: 47k; R_0805_2012Metric_Pad1.15x1.40mm_HandSolder; Digikey Part No. 311-47KARCT-ND
R58: 2.2k; R_0603_1608Metric_Pad0.98x0.95mm_HandSolder; Digikey Part No. 311-2.2KGRCT-ND
R59: 200; R_0603_1608Metric_Pad0.98x0.95mm_HandSolder; Digikey Part No. 311-200GRCT-ND
R62: 12k; R_0805_2012Metric_Pad1.15x1.40mm_HandSolder; Digikey Part No. 311-12KARCT-ND
R63: 3k; R_0603_1608Metric_Pad0.98x0.95mm_HandSolder; Digikey Part No. 311-3.0KGRCT-ND
R64, R65: 30k; R_0603_1608Metric_Pad0.98x0.95mm_HandSolder; Digikey Part No. 311-30KGRCT-ND
R66, R67: 24k; R_0805_2012Metric_Pad1.15x1.40mm_HandSolder; Digikey Part No. 311-24KARCT-ND
R68: 250; R_0603_1608Metric_Pad0.98x0.95mm_HandSolder; Digikey Part No. 13-RT0603BRE07250RLCT-ND
R69, R70: 100; R_0603_1608Metric_Pad0.98x0.95mm_HandSolder; Digikey Part No. 311-100GRCT-ND
R71: 22; R_0805_2012Metric_Pad1.15x1.40mm_HandSolder; Digikey Part No. 13-RT0805BRD0722RLCT-ND
RN1: LT5400_10k; TSSOP-8_3x3mm_P0.65mm; Digikey Part No. 505-LT5400ACMS8E-1#PBF-ND
U19, U20, U21: 6N137; DIP-8_W7.62mm_Socket; Digikey Part No. 6N137IS-ND
U22: BD9G341EFJ; HTSOP-8-1EP_3.9x4.9mm_P1.27mm_EP2.4x3.2mm_ThermalVias; Digikey Part No. BD9G341AEFJ-E2CT-ND
U23, U24: LMV358; SOIC-8_3.9x4.9mm_P1.27mm; Digikey Part No. LMV358DR2GOSCT-ND
U25: OPA2192; TSSOP-8_3x3mm_P0.65mm; Digikey Part No. 296-50480-1-ND
U26: L7805; TO-263-2; Digikey Part No. 497-1170-1-ND

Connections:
/grbl_controller/SPINDLE_DIR: U21.3 (C); also elsewhere on the board
/grbl_controller/SPINDLE_EN: U20.3 (C); also elsewhere on the board
/grbl_controller/SPINDLE_PWM: U19.3 (C); also elsewhere on the board
/spindle_cntrl/1V_REF: R66.1, U23.1, U23.2 (-)
/spindle_cntrl/5V: C47.1, R46.2, R47.2, R48.2, R51.1, R52.2, R53.2, R61.2, R62.1, U19.7 (EN), U19.8 (VCC), U20.7 (EN), U20.8 (VCC), U21.7 (EN), U21.8 (VCC), U23.8 (V+), U24.8 (V+), U26.3 (OUT)
/spindle_cntrl/12V: C43.1, C46.1, L5.2, R58.1, U26.1 (IN)
/spindle_cntrl/24V_VFD: C37.1, D47.1 (K), J17.2, R49.1, R68.1, RN1.8 (R1.2), U22.8 (VCC), U25.8 (V+)
/spindle_cntrl/GND_VFD: C37.2, C38.2, C41.2, C42.2, C43.2, C46.2, C47.2, D43.2 (A), D44.2 (A), D45.2 (A), D46.1 (K), D48.2 (A), J17.1, J19.1, Q1.2 (S), Q2.2 (S), R55.2, R56.2, R59.2, R63.2, R65.2, RN1.2 (R2.1), U19.5 (GND), U20.5 (GND), U21.5 (GND), U22.2 (GND), U23.4 (V-), U24.4 (V-), U25.4 (V-), U26.2 (GND)
unnamed: C38.1, R54.1, R57.2
unnamed: C39.1, U22.3 (VC)
unnamed: C39.2, R56.1
unnamed: C40.1, U22.7 (BST)
unnamed: C40.2, D45.1 (K), L5.1, U22.1 (LX)
unnamed: C41.1, R57.1, R60.2
unnamed: C42.1, R60.1, U23.5 (+)
unnamed: C44.1, Q3.3 (S), RN1.7 (R2.2), U25.2 (A-)
unnamed: C44.2, R69.2, U25.1 (OUT_A)
unnamed: C45.1, R70.2, U25.7 (OUT_B)
unnamed: C45.2, Q4.3 (S), R68.2, U25.6 (B-)
unnamed: D43.1 (K), Q1.1 (G), R52.1, U20.6 (VO)
unnamed: D44.1 (K), Q2.1 (G), R53.1, U21.6 (VO)
unnamed: D46.2 (A), R61.1
unnamed: D47.2 (A), D48.1 (K), Q4.2 (D), R71.1
unnamed: J18.1, Q1.3 (D)
unnamed: J18.2, Q2.3 (D)
unnamed: J19.2, R71.2
unnamed: Q3.1 (G), R69.1
unnamed: Q3.2 (D), RN1.1 (R1.1), U25.5 (B+)
unnamed: Q4.1 (G), R70.1
unnamed: R46.1, U19.2 (A)
unnamed: R47.1, U20.2 (A)
unnamed: R48.1, U21.2 (A)
unnamed: R49.2, U22.6 (EN)
unnamed: R51.2, R54.2, U19.6 (VO)
unnamed: R55.1, U22.5 (RT)
unnamed: R58.2, R59.1, U22.4 (FB)
unnamed: R62.2, R63.1, U23.3 (+)
unnamed: R64.1, R66.2, U24.5 (+)
unnamed: R64.2, U23.6 (-), U23.7
unnamed: R65.1, R67.2, U24.6 (-)
unnamed: R67.1, U24.7, U25.3 (A+)

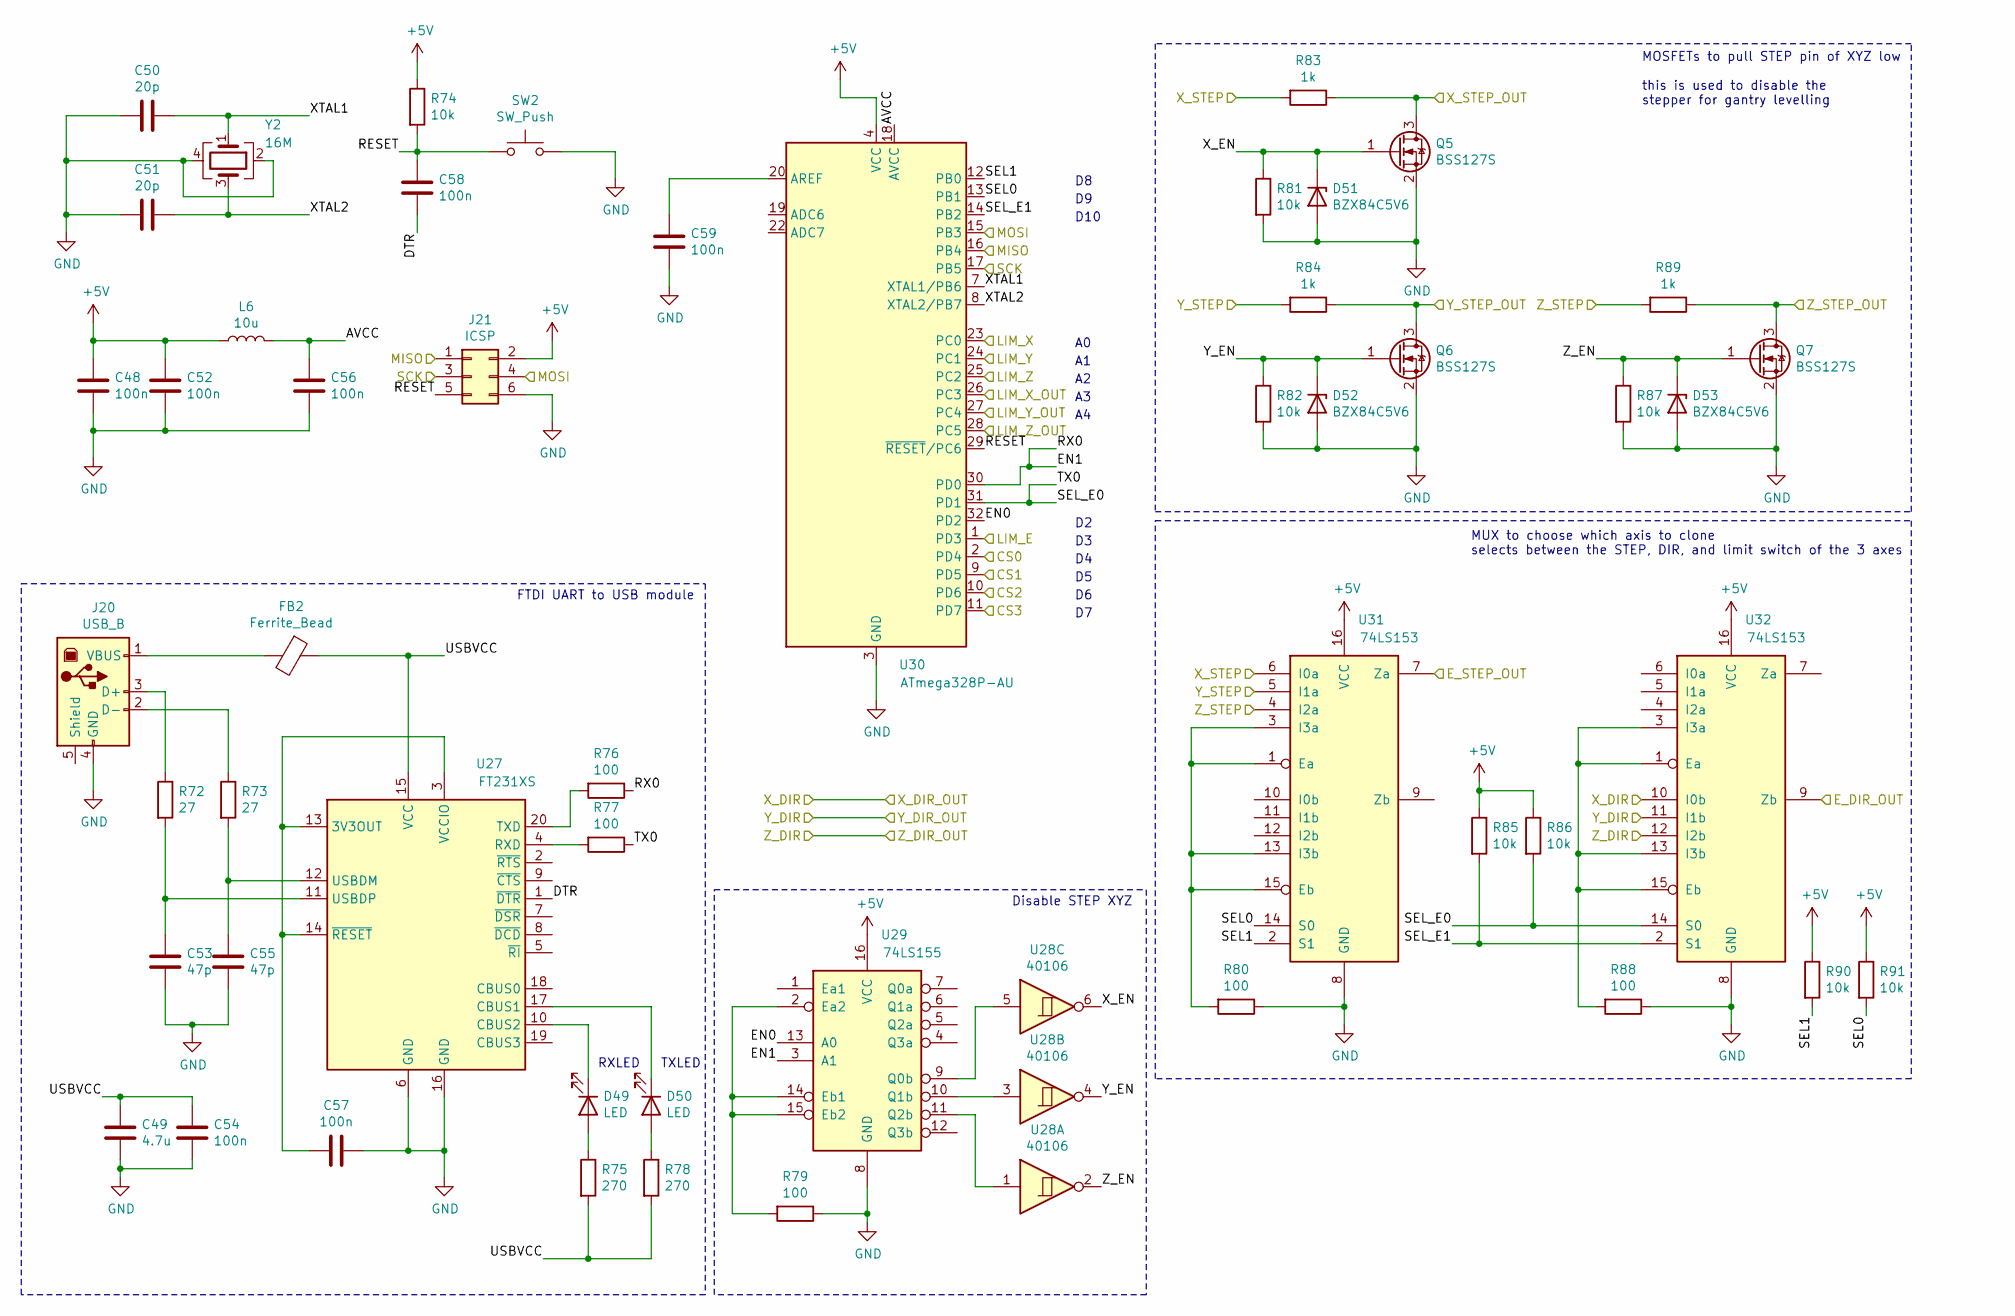
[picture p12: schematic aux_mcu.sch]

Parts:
C48, C52, C54, C56, C57, C58, C59: 100n; C_0603_1608Metric_Pad1.05x0.95mm_HandSolder; Digikey Part No. 1276-1941-1-ND
C49: 4.7u; C_1206_3216Metric_Pad1.33x1.80mm_HandSolder; Digikey Part No. 1276-6781-1-ND
C50, C51: 20p; C_0603_1608Metric_Pad1.05x0.95mm_HandSolder; Digikey Part No. 1276-1187-1-ND
C53, C55: 47p; C_0402_1005Metric_Pad0.74x0.62mm_HandSolder; Digikey Part No. 1276-1699-1-ND
D49, D50: LED; LED_1206_3216Metric_Pad1.42x1.75mm_HandSolder; Digikey Part No. 404-1042-1-ND
D51, D52, D53: BZX84C5V6; D_SOT-23_ANK; Digikey Part No. 1514-BZX84C5V6TRPBFREECT-ND
FB2: Ferrite_Bead; C_0603_1608Metric_Pad1.05x0.95mm_HandSolder; Digikey Part No. 732-1591-1-ND
J20: USB_B; USB_B_OST_USB-B1HSxx_Horizontal; Digikey Part No. 380-1492-ND
J21: ICSP; PinHeader_2x03_P2.54mm_Vertical; Digikey Part No. 609-3234-ND
L6: 10u; L_0805_2012Metric_Pad1.05x1.20mm_HandSolder; Digikey Part No. 490-4029-1-ND
Q5, Q6, Q7: BSS127S; SOT-23; Digikey Part No. BSS127S-7DICT-ND
R72, R73: 27; R_0603_1608Metric_Pad0.98x0.95mm_HandSolder; Digikey Part No. 311-27GRCT-ND
R74, R81, R82, R85, R86, R87, R90, R91: 10k; R_0805_2012Metric_Pad1.15x1.40mm_HandSolder; Digikey Part No. 311-10KARCT-ND
R75, R78: 270; R_0805_2012Metric_Pad1.15x1.40mm_HandSolder; Digikey Part No. YAG6172CT-ND
R76, R77, R79, R80, R88: 100; R_0603_1608Metric_Pad0.98x0.95mm_HandSolder; Digikey Part No. 311-100GRCT-ND
R83, R84, R89: 1k; R_1206_3216Metric_Pad1.30x1.75mm_HandSolder; Digikey Part No. 311-1.0KERCT-ND
SW2: SW_Push; SW_Push_1P1T_NO_6x6mm_H9.5mm; Digikey Part No. EG2526CT-ND
U27: FT231XS; SSOP-20_3.9x8.7mm_P0.635mm; Digikey Part No. 768-1129-1-ND
U28: 40106; TSSOP-14_4.4x5mm_P0.65mm; Digikey Part No. HEF40106BTT,112-ND
U29: 74LS155; SOIC-16_3.9x9.9mm_P1.27mm; Digikey Part No. 296-33960-5-ND
U30: ATmega328P-AU; TQFP-32_7x7mm_P0.8mm; Digikey Part No. ATMEGA328P-AU-ND
U31, U32: 74LS153; SOIC-16_3.9x9.9mm_P1.27mm; Digikey Part No. 296-3653-5-ND
Y2: 16M; Crystal_SMD_SeikoEpson_TSX3225-4Pin_3.2x2.5mm_HandSoldering; Digikey Part No. SER4372CT-ND

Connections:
+5V: C48.1, C52.1, J21.2, L6.1, R74.1, R85.1, R86.1, R90.1, R91.1, U29.16 (VCC), U30.4 (VCC), U30.6 (VCC), U31.16 (VCC), U32.16 (VCC); also elsewhere on the board
/CS_E: U30.11 (PD7); also elsewhere on the board
/CS_X: U30.2 (PD4); also elsewhere on the board
/CS_Y: U30.9 (PD5); also elsewhere on the board
/CS_Z: U30.10 (PD6); also elsewhere on the board
/MISO: J21.1, U30.16 (PB4); also elsewhere on the board
/MOSI: J21.4, U30.15 (PB3); also elsewhere on the board
/SCK: J21.3, U30.17 (PB5); also elsewhere on the board
/aux_mcu/AVCC: C56.1, L6.2, U30.18 (AVCC)
/aux_mcu/DTR: C58.2, U27.1 (~DTR)
/aux_mcu/EN0: U29.13 (A0), U30.32 (PD2)
/aux_mcu/EN1: R76.1, U29.3 (A1), U30.30 (PD0)
/aux_mcu/LIM_E: U30.1 (PD3); also elsewhere on the board
/aux_mcu/LIM_X: U30.23 (PC0); also elsewhere on the board
/aux_mcu/LIM_Y: U30.24 (PC1); also elsewhere on the board
/aux_mcu/LIM_Z: U30.25 (PC2); also elsewhere on the board
/aux_mcu/RESET: C58.1, J21.5, R74.2, SW2.1, U30.29 (~RESET~/PC6)
/aux_mcu/SEL0: R91.2, U30.13 (PB1), U31.14 (S0)
/aux_mcu/SEL1: R90.2, U30.12 (PB0), U31.2 (S1)
/aux_mcu/SEL_E0: R77.1, R86.2, U30.31 (PD1), U32.14 (S0)
/aux_mcu/SEL_E1: R85.2, U30.14 (PB2), U32.2 (S1)
/aux_mcu/USBVCC: C49.1, C54.1, FB2.1, R75.2, R78.2, U27.15 (VCC)
/aux_mcu/XTAL1: C50.1, U30.7 (XTAL1/PB6), Y2.1
/aux_mcu/XTAL2: C51.1, U30.8 (XTAL2/PB7), Y2.3
/aux_mcu/X_EN: D51.1 (K), Q5.1 (G), R81.1, U28.6
/aux_mcu/Y_EN: D52.1 (K), Q6.1 (G), R82.1, U28.4
/aux_mcu/Z_EN: D53.1 (K), Q7.1 (G), R87.1, U28.2
/grbl_controller/DIR_X: U32.10 (I0b); also elsewhere on the board
/grbl_controller/DIR_Y: U32.11 (I1b); also elsewhere on the board
/grbl_controller/DIR_Z: U32.12 (I2b); also elsewhere on the board
/grbl_controller/LIM_X: U30.26 (PC3); also elsewhere on the board
/grbl_controller/LIM_Y: U30.27 (PC4); also elsewhere on the board
/grbl_controller/LIM_Z: U30.28 (PC5); also elsewhere on the board
/grbl_controller/STEP_X: R83.2, U31.6 (I0a); also elsewhere on the board
/grbl_controller/STEP_Y: R84.2, U31.5 (I1a); also elsewhere on the board
/grbl_controller/STEP_Z: R89.2, U31.4 (I2a); also elsewhere on the board
/stepper_drivers/E_DIR: U32.9 (Zb); also elsewhere on the board
/stepper_drivers/E_STEP: U31.7 (Za); also elsewhere on the board
/stepper_drivers/X_STEP: Q5.3 (D), R83.1; also elsewhere on the board
/stepper_drivers/Y_STEP: Q6.3 (D), R84.1; also elsewhere on the board
/stepper_drivers/Z_STEP: Q7.3 (D), R89.1; also elsewhere on the board
GND: C48.2, C49.2, C50.2, C51.2, C52.2, C53.2, C54.2, C55.2, C56.2, C57.1, C59.2, D51.2 (A), D52.2 (A), D53.2 (A), J20.4 (GND), J21.6, Q5.2 (S), Q6.2 (S), Q7.2 (S), R79.1, R80.1, R81.2, R82.2, R87.2, R88.1, SW2.2, U27.6 (GND), U27.16 (GND), U29.8 (GND), U30.3 (GND), U30.5 (GND), U30.21 (GND), U31.8 (GND), U32.8 (GND), Y2.2, Y2.4; also elsewhere on the board
unnamed: C53.1, R72.2, U27.11 (USBDP)
unnamed: C55.1, R73.2, U27.12 (USBDM)
unnamed: C57.2, U27.3 (VCCIO), U27.13 (3V3OUT), U27.14 (~RESET)
unnamed: C59.1, U30.20 (AREF)
unnamed: D49.1 (K), U27.10 (CBUS2)
unnamed: D49.2 (A), R75.1
unnamed: D50.1 (K), U27.17 (CBUS1)
unnamed: D50.2 (A), R78.1
unnamed: FB2.2, J20.1 (VBUS)
unnamed: J20.2 (D-), R73.1
unnamed: J20.3 (D+), R72.1
unnamed: R76.2, U27.20 (TXD)
unnamed: R77.2, U27.4 (RXD)
unnamed: R79.2, U29.2 (Ea2), U29.14 (Eb1), U29.15 (Eb2)
unnamed: R80.2, U31.1 (Ea), U31.3 (I3a), U31.13 (I3b), U31.15 (Eb)
unnamed: R88.2, U32.1 (Ea), U32.3 (I3a), U32.13 (I3b), U32.15 (Eb)
unnamed: U28.1, U29.11 (Q2b)
unnamed: U28.3, U29.10 (Q1b)
unnamed: U28.5, U29.9 (Q0b)

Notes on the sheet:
D10
TXLED
RXLED
FTDI UART to USB module
Disable STEP XYZ
MOSFETs to pull STEP pin of XYZ low this is used to disable the stepper for gantry levelling
MUX to choose which axis to clone selects between the STEP, DIR, and limit switch of the 3 axes

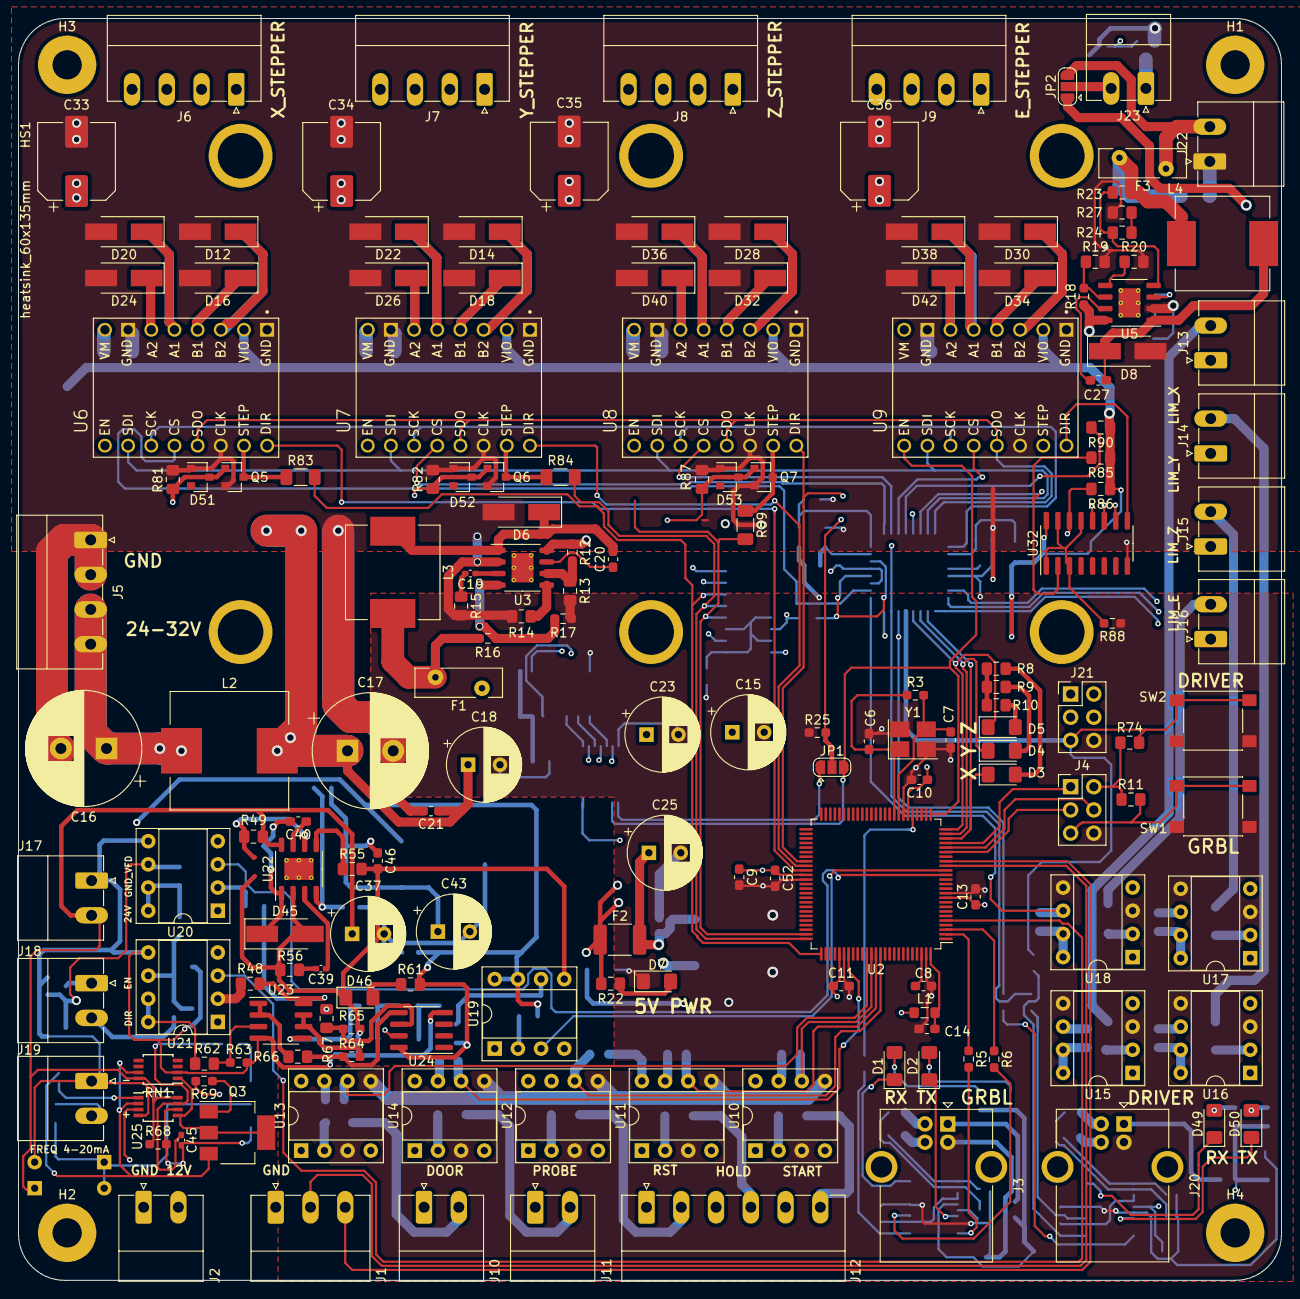
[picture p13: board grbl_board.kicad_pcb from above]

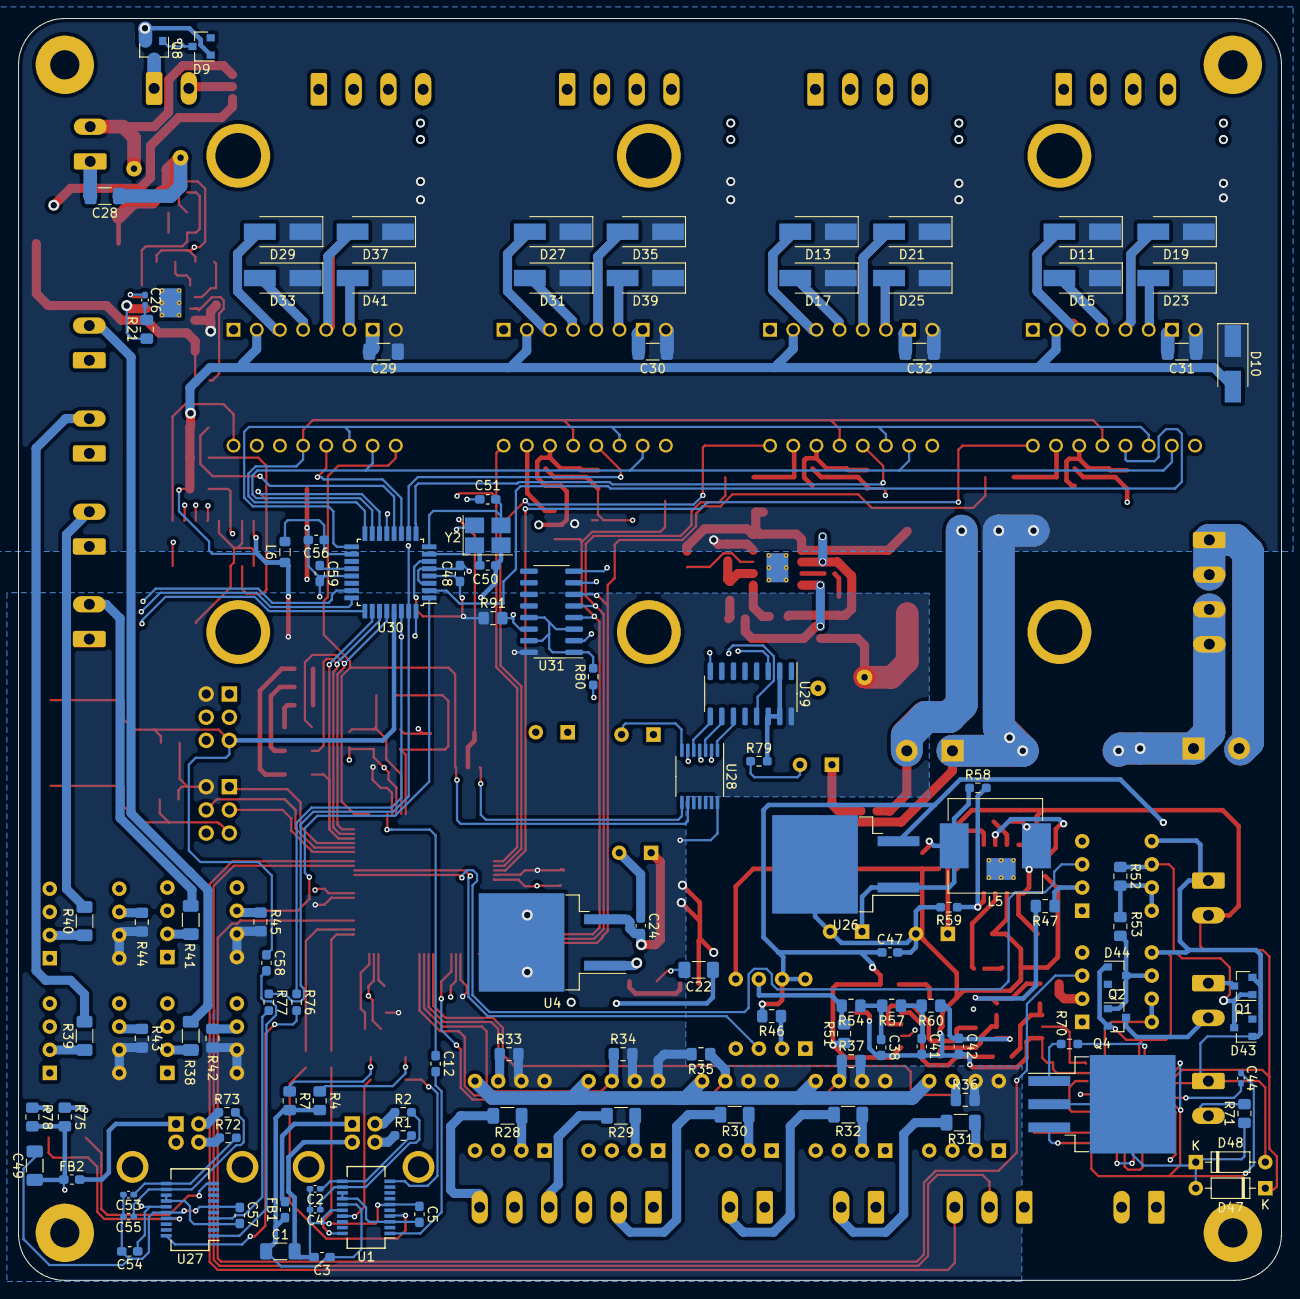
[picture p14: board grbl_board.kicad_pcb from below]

Board: 4 copper layers, 138.4 x 138.3 mm, 287 parts (113 on the bottom side), 199 nets.

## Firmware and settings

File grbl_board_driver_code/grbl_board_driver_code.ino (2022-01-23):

#include <TMCStepper.h>

//#define TMCSTEPPER

#define CLONED_AXIS           1  //0:x, 1:y, 2:z
#define LIMIT_INVERT       false

// stepper motor config
#define MICROSTEPS            0
#define CURRENT_MA         2500
#define HOLD_MULTIPLIER     0.8
#define INTERPOLATE        true

#define STEALTHCHOP       false

// experimental
//#define SQUARE_WAVE_STEPPING

#define CHOPPER_TIMING {4, -2, 1}

#define LIM_X_IN     A0
#define LIM_Y_IN     A1
#define LIM_Z_IN     A2

#define LIM_X_OUT    A3
#define LIM_Y_OUT    A4
#define LIM_Z_OUT    A5

#define LIM_E        3

#define EN0 2
#define EN1 0

#define SEL0 9
#define SEL1 8

#define SEL_E0 1
#define SEL_E1 10

#define CS_X 4
#define CS_Y 5
#define CS_Z 6
#define CS_E 7

uint8_t lim_e_val = 0, lim_cloned_val = 0;
boolean pulloff = false;
long levelling = -1;

#define R_SENSE 0.075f // Match to your driver
                      // SilentStepStick series use 0.11
                      // UltiMachine Einsy and Archim2 boards use 0.2
                      // Panucatt BSD2660 uses 0.1
                      // Watterott TMC5160 uses 0.075

typedef struct {
  uint8_t toff;    // [1..15]
  int8_t hend;     // [-3..12]
  uint8_t hstrt;   // [1..8]
} chopper_timing_t;

#ifdef TMCSTEPPER
  TMC5160Stepper x_stepper(CS_X, R_SENSE);
  TMC5160Stepper y_stepper(CS_Y, R_SENSE);
  TMC5160Stepper z_stepper(CS_Z, R_SENSE);
  TMC5160Stepper e_stepper(CS_E, R_SENSE);
  
  TMC5160Stepper steppers[] = {x_stepper, y_stepper, z_stepper, e_stepper};
  int8_t timings[] = CHOPPER_TIMING; // Default 4, -2, 1
  static constexpr chopper_timing_t chop_init = CHOPPER_TIMING;
#endif
int8_t enable = LOW , disable = HIGH;


void stopStepper(int num) {
  digitalWrite(EN0, num&0x1);
  digitalWrite(EN1, (num&0x2) >> 1);
}

void selectStepClone(int num) {
  digitalWrite(SEL0, num&0x1);
  digitalWrite(SEL1, (num&0x2) >> 1);
}

void selectAxisClone(int num) {
  digitalWrite(SEL_E0, num&0x1);
  digitalWrite(SEL_E1, (num&0x2) >> 1);
}

void setup() {
  pinMode(SEL0, OUTPUT);
  pinMode(SEL1, OUTPUT);
  pinMode(SEL_E0, OUTPUT);
  pinMode(SEL_E1, OUTPUT);
  pinMode(EN0, OUTPUT);
  pinMode(EN1, OUTPUT);
  
  pinMode(LIM_X_OUT, OUTPUT);
  pinMode(LIM_Y_OUT, OUTPUT);
  pinMode(LIM_Z_OUT, OUTPUT);

  pinMode(LIM_X_IN, INPUT_PULLUP);
  pinMode(LIM_Y_IN, INPUT_PULLUP);
  pinMode(LIM_Z_IN, INPUT_PULLUP);

  pinMode(LIM_E, INPUT_PULLUP);

  pinMode(CS_X, OUTPUT);
  pinMode(CS_Y, OUTPUT);
  pinMode(CS_Z, OUTPUT);
  pinMode(CS_E, OUTPUT);

  if (LIMIT_INVERT) {
    enable = HIGH;
    disable = LOW;
  }

  #ifdef TMCSTEPPER
    SPI.begin();
    
    for (auto& st: steppers){
      st.begin();                 //  SPI: Init CS pins and possible SW SPI pins
      st.reset();
      st.toff(0);
      st.push();
      st.toff(chop_init.toff);
      
      CHOPCONF_t chopconf{0};
      chopconf.tbl = 0b01;
      chopconf.toff = chop_init.toff;
      chopconf.intpol = INTERPOLATE;
      chopconf.hend = chop_init.hend + 3;
      chopconf.hstrt = chop_init.hstrt - 1;
      #ifdef SQUARE_WAVE_STEPPING
        chopconf.dedge = true;
      #endif
      st.CHOPCONF(chopconf.sr);
      
      st.rms_current(CURRENT_MA, HOLD_MULTIPLIER);
      st.microsteps(MICROSTEPS);
      st.iholddelay(10);
      st.TPOWERDOWN(128); // ~2s until driver lowers to hold current
      
      st.en_pwm_mode(STEALTHCHOP); // Toggle stealthChop on TMC2130/2160/5130/5160
      st.TPWMTHRS(500);   
      st.TCOOLTHRS(0xFFFFF); // 20bit max - Lower velocity threshold for switching on CoolStep and stop on stall. Below this velocity CoolStep becomes disabled (not used in STEP/DIR mode). Adapt to the lower limit of the velocity range where StallGuard2 gives a stable result.
      st.THIGH(0);    // Upper velocity threshold value for CoolStep and stop on stall. Above this velocity CoolStep becomes disabled. Adapt to the velocity range where StallGuard2 gives a stable result.
      st.semin(5);    // [0-15] If the StallGuard2 result falls below SEMIN*32, the motor current becomes increased to reduce motor load angle. 0 = smart current control CoolStep off
      st.semax(2);    // [0-15] If the StallGuard2 result is equal to or above (SEMIN+SEMAX+1)*32, the motor current becomes decreased to save energy.
      st.sedn(0b01);  // For each 8 StallGuard2 values decrease by one
     
      TMC2160_n::PWMCONF_t pwmconf{0};
      pwmconf.pwm_lim = 12;
      pwmconf.pwm_reg = 8;
      pwmconf.pwm_autograd = true;
      pwmconf.pwm_autoscale = true;
      pwmconf.pwm_freq = 0b01;
      pwmconf.pwm_grad = 14;
      pwmconf.pwm_ofs = 36;
      st.PWMCONF(pwmconf.sr);
      st.drvstrength(0b11);   // 00: weak  01: weak+TC (medium above OTPW level)  10: medium  11: strong  
  
      st.sfilt(true);
      
      st.GSTAT(); // Clear GSTAT
      st.RAMP_STAT();
  
    }
  #else
    pinMode(11, OUTPUT);
    pinMode(12, OUTPUT);
    pinMode(13, OUTPUT);
  
    digitalWrite(11, LOW);
    digitalWrite(12, HIGH);
    digitalWrite(13, LOW);
    
    digitalWrite(CS_X, LOW);
    digitalWrite(CS_Y, LOW);
    digitalWrite(CS_Z, LOW);
    digitalWrite(CS_E, LOW);
  #endif
  
  stopStepper(3);
  selectStepClone(CLONED_AXIS);
  selectAxisClone(CLONED_AXIS);
}

void loop() {
  switch(CLONED_AXIS) {
    case 0: 
    digitalWrite(LIM_Y_OUT, digitalRead(LIM_Y_IN));
    digitalWrite(LIM_Z_OUT, digitalRead(LIM_Z_IN));
    lim_cloned_val = digitalRead(LIM_X_IN);
    break;
    case 1: 
    digitalWrite(LIM_X_OUT, digitalRead(LIM_X_IN));
    digitalWrite(LIM_Z_OUT, digitalRead(LIM_Z_IN));
    lim_cloned_val = digitalRead(LIM_Y_IN);
    break;
    case 2: 
    digitalWrite(LIM_X_OUT, digitalRead(LIM_X_IN));
    digitalWrite(LIM_Y_OUT, digitalRead(LIM_Y_IN));
    lim_cloned_val = digitalRead(LIM_Z_IN);
    break;
    default: break;
  }
  
  lim_e_val = digitalRead(LIM_E);
  if (lim_e_val != lim_cloned_val && !pulloff && !(levelling >= 0 && millis()-levelling < 3000)) {
    switch(CLONED_AXIS) {
      case 0: digitalWrite(LIM_X_OUT, enable); break;
      case 1: digitalWrite(LIM_Y_OUT, enable); break;
      case 2: digitalWrite(LIM_Z_OUT, enable); break;
      default: break;
    }
    if (lim_cloned_val == disable) stopStepper(CLONED_AXIS);
    if (lim_e_val == disable) selectStepClone(3);
    if (levelling <0) levelling = millis();
  } else if (lim_e_val == lim_cloned_val) {
    stopStepper(3);
    selectStepClone(CLONED_AXIS);
    if (lim_e_val == enable) {
      pulloff = false;
      switch(CLONED_AXIS) {
        case 0: digitalWrite(LIM_X_OUT, enable); break;
        case 1: digitalWrite(LIM_Y_OUT, enable); break;
        case 2: digitalWrite(LIM_Z_OUT, enable); break;
        default: break;
      }
    } else {
      pulloff = true;
      switch(CLONED_AXIS) {
        case 0: digitalWrite(LIM_X_OUT, disable); break;
        case 1: digitalWrite(LIM_Y_OUT, disable); break;
        case 2: digitalWrite(LIM_Z_OUT, disable); break;
        default: break;
      }
    } 
  } else if (levelling >= 0 && millis()-levelling < 3000) {
    switch(CLONED_AXIS) {
      case 0: digitalWrite(LIM_X_OUT, disable); break;
      case 1: digitalWrite(LIM_Y_OUT, disable); break;
      case 2: digitalWrite(LIM_Z_OUT, disable); break;
      default: break;
    }
  }
  
}

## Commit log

2021-10-26 created project
    [grbl_board.kicad_pcb, grbl_board.sch, grbl_controller.sch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]
2021-10-28 finished GRBL controller
    [grbl_board.sch, grbl_controller.sch, power_supply.sch]
2021-10-28 power supply stage
    [grbl_board.sch, power_supply.sch]
2021-10-28 motor driver and mcu and limit switches
    [aux_mcu.sch, grbl_board.sch, grbl_controller.sch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]
2021-10-28 changed limit switch control
    [aux_mcu.sch, grbl_board.sch, grbl_controller.sch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]
2021-10-28 spindle control stage (not complete)
    [power_supply.sch, spinlde_cntrl.sch, switch_inputs.sch]
2021-10-28 spindle control stage
    [grbl_board.sch, spinlde_cntrl.sch, stepper_drivers.sch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]
2021-10-29 edited motor outputs
    [aux_mcu.sch, grbl_controller.sch]
2021-10-30 changed to matched resistor
    [aux_mcu.sch, grbl_controller.sch, spinlde_cntrl.sch]
2021-10-30 added some footprint associations
    [aux_mcu.sch, grbl_board.sch, grbl_controller.sch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]
2021-10-30 complete footprint associations
    [aux_mcu.sch, grbl_controller.sch, power_supply.sch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]
2021-10-30 fixed mismatch for 6n137
    [aux_mcu.sch, spinlde_cntrl.sch, stepper_drivers.sch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]
2021-10-31 routing done
    [aux_mcu.sch, grbl_board.kicad_pcb, grbl_board.sch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]
2021-11-01 added connector labels and tmc 3d model
    [SilentStepStick.step, grbl_board.kicad_pcb]
2021-11-01 added usb 3d model and fixed footprint associations
    [USB_B_Horizontal.stp, aux_mcu.sch, grbl_board.kicad_pcb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]
2021-11-01 tidy up
    [stepper_drivers.sch]
2021-11-03 added more filtering caps
    [grbl_board.kicad_pcb, stepper_drivers.sch]
2021-11-04 added some descriptions in the schematic and added gerber file
    [aux_mcu.sch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]
2021-11-04 fixed limit switch disconnect issue
    [aux_mcu.sch, grbl_board.kicad_pcb, grbl_board.sch]
2021-11-05 fixed copper fill
    [aux_mcu.sch, grbl_board.kicad_pcb]
2021-11-09 added GRBL board stepper driver init and gantry level code
2021-12-12 fixed pullup resistors on board, and 5v regulator overheating, and stepper driver flipped
    [grbl_board.kicad_pcb, grbl_board.sch, power_supply.sch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]
2021-12-12 moved connectors further out
    [grbl_board.kicad_pcb]
2021-12-12 added limit switch indicator LEDs
    [grbl_board.kicad_pcb, grbl_controller.sch, switch_inputs.sch]
2022-01-23 updated board with 24V reg
    [aux_mcu.sch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]
